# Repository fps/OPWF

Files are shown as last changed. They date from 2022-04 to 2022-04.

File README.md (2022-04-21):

# Introduction

This repository contains firmware for a pickup winder based on a Ramps 1.4 board, RepRapDiscount Full Graphics Smart Controller, a 200 steps per revolution stepper motor, a servo and an Arduino Mega 2560 microcontroller board.

[Video showing the winder in action](https://www.youtube.com/shorts/mcej-a_-2Q8)

# Installation

- Assemble the pickup winder as can be seen in the picture below
- Use e.g. the Arduino IDE to flash the sketch in the src/ directory to the Mega 2560

Assembled winder

# Assembly

- 3d print the motor holder and pickup attachment plate (or think about an alternative way to secure the motor - I successfully used some blocks of wood and some double sided tape)
- Cut a piece of wood to approximately 20 cm by 20 cm that serves as the base
- Mount the arduino Mega 2560 in the back left corner using ca. two wood screws
- Mount the Ramps 1.4 board on top of the Arduino
- Attach at least the Z-direction stepper driver and set it to 4 microsteps using the jumpers before inserting the driver board.
- Set the jumper on the Ramps board to supply 5V power to the servo (That jumper is left of the reset button on the board)
- Attach the servo to the second servo pin from the left (it's the one corresponding to the digital pin D6 - this is important for the PWM and interrupt management)
- Secure the servo cable a little bit with a piece of tape so that it won't entangle with the pickup wire
- Attach the servo on a piece of wood to raise it up a little from the base board. Position it in such a way that the center of the servo axis aligns with the center of a pickup bobbin when attached to the motor
- At the front right attach two felt-padded pieces of wood with 2 screws. These serve as pickup wire tensioner. 
- Figure out a way to connect your stepper motor to the corresponding pins on the Ramps board
- Secure the stepper motor cables with some tape so that they don't entangle with the pickup wire
- Mount the display using two wood screws, but screw them in at an angle. The back of the display will be held by the flat cables.

# Usage

## General

- Press the encoder button on the display to enter/leave a setting
- Rotate the encoder to change a setting. Since the display is so godawfully slow the code waits for a timeout until updating the display.
- Press the STOP button on the display to start the winding process
- Press the STOP button to stop the winding process, too ;)
- Press the STOP button twice (doubleclick) to reset the "Current Winds" counter to 0

## Menu entries

- Target winds: The number of winds that the winder will stop winding at. Note that you can change this at any point. So to wind for e.g. 1000 winds and then another 1000 winds first set the target winds to 1000, start the winding, and after it stopped set the target to 2000 and start the winding again.
- Current winds: The current number of winds performed since the counter was last reset
- Wind direction: Can be either 1 or -1 corresponding to either clockwise/anticlockwise or anticlockwise/clockwise directions depending on how you wired the stepper motor
- Speed W/s: The speed in winds per second
- Acceleration W/s^2: The acceleration used to ramp up to the selected speed
- Winds/Sweep: The number of winds performed for a full servo sweep. So if you select 100 here, the servo will be swept from Right limit to Left limit during the first 50 winds and from Left limit to Right limit during the second 50 sweeps. Then the dance starts all over.
- Right limit deg.: The first servo limit 
- Left limit deg. The second servo limit

# CAVEATS

- The button handling is done purely in software without interrupts, so sometimes presses are missed.

# LICENSE

- To be figured out

# Author

- Florian Paul Schmidt
- Florian Hofmann

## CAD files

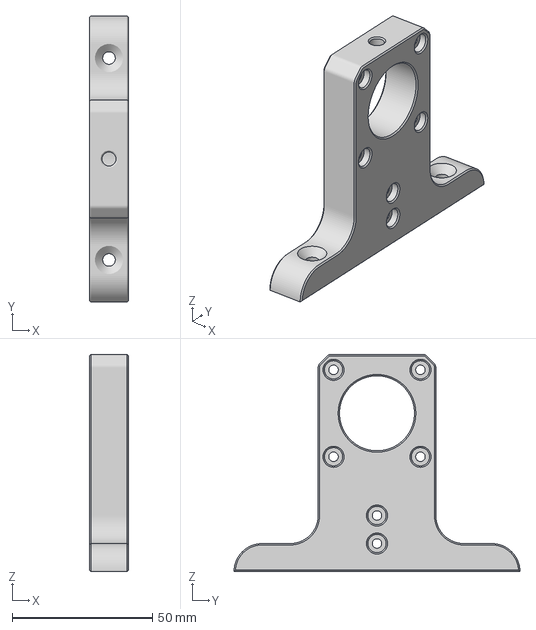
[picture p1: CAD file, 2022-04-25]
hardware/3mf/MotorMount.3mf
14.0 x 102.0 x 77.5 mm

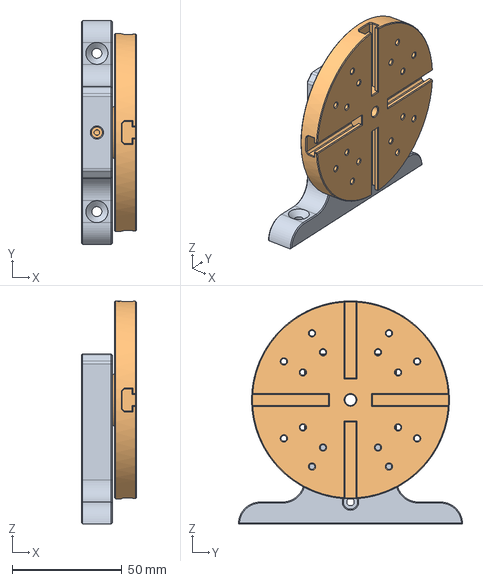
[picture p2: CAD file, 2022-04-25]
hardware/step/Mini-Lathe v3.step
25.0 x 102.0 x 101.5 mm

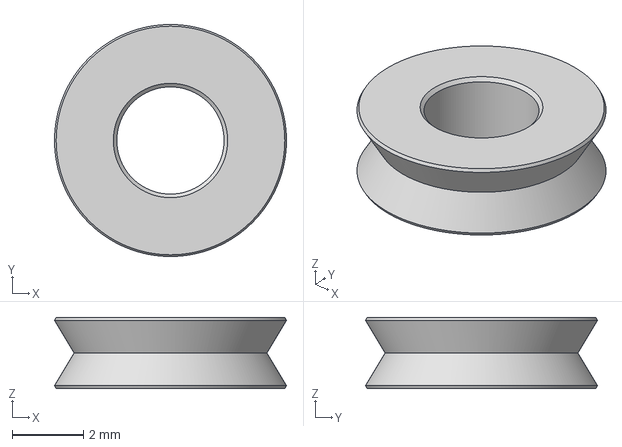
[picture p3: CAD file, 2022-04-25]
hardware/3mf/Guide Ring.3mf
6.50 x 6.50 x 2.00 mm

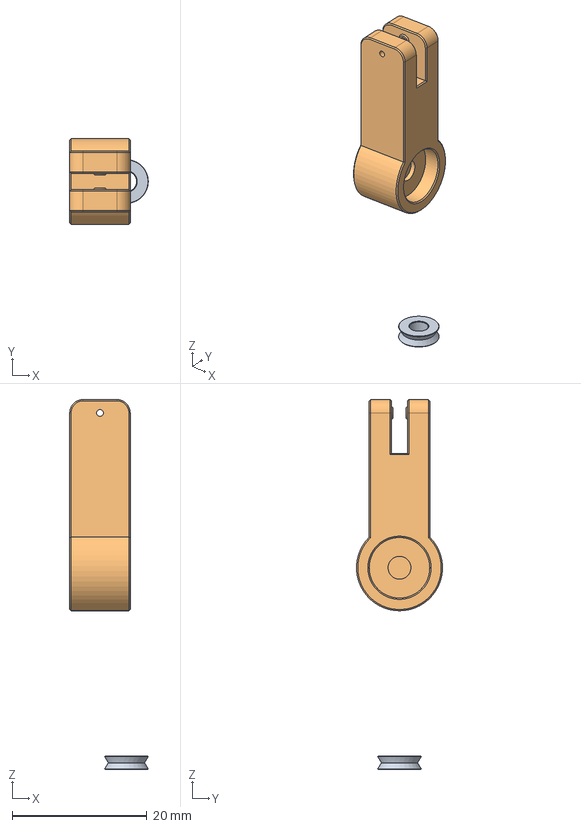
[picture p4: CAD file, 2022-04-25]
hardware/step/Roller v2.step
11.7 x 12.8 x 55.0 mm
Guide Ring
Guide Arm

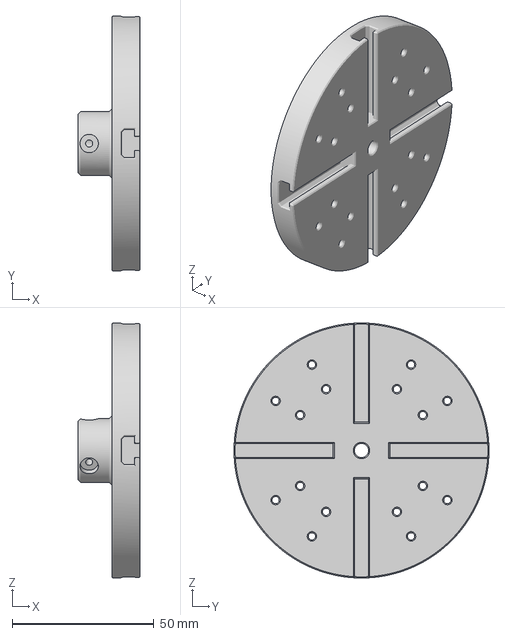
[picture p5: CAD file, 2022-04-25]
hardware/3mf/FrontPlate.3mf
22.0 x 90.0 x 90.0 mm

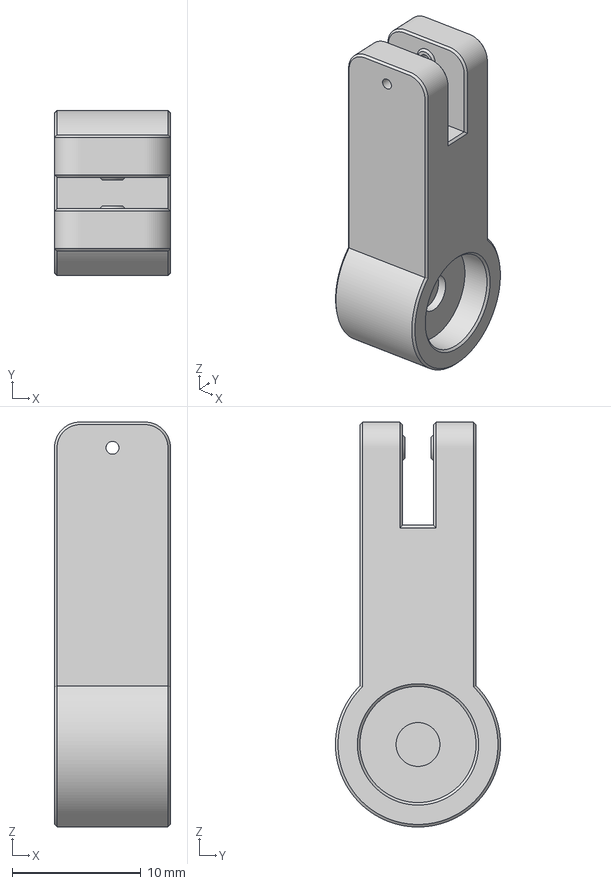
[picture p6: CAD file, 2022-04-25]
hardware/3mf/Guide Arm.3mf
9.00 x 12.8 x 31.4 mm

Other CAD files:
hardware/stl/FrontPlate.stl
hardware/stl/Guide Arm.stl
hardware/stl/Guide Ring.stl
hardware/stl/MotorMount.stl

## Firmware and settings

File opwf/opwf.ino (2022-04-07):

#define ENCODER_USE_INTERRUPTS
#include <EncoderButton.h>

#include <Button2.h>
#include <Servo_Hardware_PWM.h>
#include <EEPROM.h>
#include <U8g2lib.h>

// #################### CONSTANTS

#define STOP_BUTTON 41

#define ENCODER_PUSH_BUTTON 35
#define ENCODER_BUTTON1 31 
#define ENCODER_BUTTON2 33

#define MOTOR_Z_ENABLE 38
#define MOTOR_Z_DIRECTION 55
#define MOTOR_Z_STEP 54

#define SERVO_PIN 6

const long stepper_timer_period_usec = 20L;
const long servo_timer_period_usec = 10e3L;

const long steps_per_turn = 200L;
const long microsteps = 16L;


// #################### GLOBAL STATE

long step_period_usec = 0;
unsigned long steps_per_second;
long elapsed_since_step_usec = 0L;


unsigned long steps_per_second_limit = 1L;
volatile long max_steps = 1L;
volatile long steps_taken = 0L;

// volatile bool start_active = false;
long start_time_usec = 0;


// #################### SERVO

Servo servo;


// #################### BUTTONS

Button2 encoder_push_button;
Button2 stop_button;

volatile enum {
  STOPPED = 0,
  STARTING,
  RUNNING,
  STOPPING
} state;


// #################### MENU

U8G2_ST7920_128X64_F_SW_SPI u8g(U8G2_R0, 23, 17, 16);

struct menu_item {
  const char* text;
  float value;
  float increment;
  float minimum;
  float maximum;
};

enum menu_entry_indices {
  TARGET_WINDS = 0,
  CURRENT_WINDS,
  WIND_DIRECTION,
  SPEED,
  ACCELERATION,
  WINDS_PER_SWEEP,
  RIGHT_LIMIT,
  LEFT_LIMIT,
  NUMBER_OF_MENU_ENTRIES
};

int current_menu_entry_index = 0;
bool menu_needs_redraw = false;

menu_item menu[NUMBER_OF_MENU_ENTRIES] = {
  { "Target Winds     ",    1000,  50,     0, 20000 },
  { "Current Winds    ",       0,   0,     0, 20000 },
  { "Wind Direction   ",       1,   2,    -1,     1 },
  { "Speed W/s        ",       2,   0.1, 0.1,    10 },
  { "Accel. W/s^2     ",     1.0,   0.1, 0.1,    10 },
  { "Winds/Sweep      ",     100,  10,     0,  5000 },
  { "Right limit deg. ",      90,   1,     0,   180 },
  { "Left Limit deg.  ",     120,   1,     0,   180 }
};

bool menu_data_entry_active = false;

EncoderButton encoder(ENCODER_BUTTON1, ENCODER_BUTTON2);

void draw_menu() {
  u8g.firstPage();
  do {
    byte y_position = 7;
    const byte y_spacing = 8;
    u8g.setFont(u8g2_font_5x7_mr);
    for (byte menu_entry_index = 0; menu_entry_index < NUMBER_OF_MENU_ENTRIES; ++menu_entry_index) {  
      u8g.setDrawColor(2);
      if (menu_entry_index == current_menu_entry_index && !menu_data_entry_active) {
        u8g.setDrawColor(0);    
      }
      u8g.setCursor(0, y_position);
      u8g.print(menu[menu_entry_index].text); 
      
      if (menu_entry_index == current_menu_entry_index && menu_data_entry_active) {
        u8g.setDrawColor(0);    
      }
      char buffer[10];
      dtostrf(menu[menu_entry_index].value, 8, 2, buffer);
      u8g.print(buffer);    
      y_position += y_spacing;      
    }
  } while ( u8g.nextPage() );  
}


// #################### EEPROM

const float magic_cookie = 331.337f;

void read_eeprom() {
  Serial.println("Restoring from EEPROM...");
  for (unsigned index = 0; index < NUMBER_OF_MENU_ENTRIES; ++index) {
    EEPROM.get((index+1)*sizeof(float), menu[index].value);
  }
  Serial.println("Done.");
}

void save_eeprom() {
  Serial.println("Saving to EEPROM");
  EEPROM.put(0, magic_cookie);
  float eeprom_value;
  for (unsigned index = 0; index < NUMBER_OF_MENU_ENTRIES; ++index) {
    EEPROM.get((index+1)*sizeof(float), eeprom_value);
    if (eeprom_value != menu[index].value) {
      Serial.println(menu[index].value);
      EEPROM.put((index+1)*sizeof(float), menu[index].value);      
    }
  }
  Serial.println("Done.");
}


// #################### SETUP

void setup() {
  Serial.begin(115200);
  while (!Serial) {}

  Serial.println("Open Pickup Winder Firmware v0.1 starting up...");

  Serial.println("Setting up EEPROM...");
  
  float eeprom_value;
  if (EEPROM.get(0, eeprom_value) == magic_cookie) {
    read_eeprom();
  } else {
    save_eeprom(); 
  }

  Serial.println("Setting up pins...");
  
  pinMode(37, OUTPUT);

  // Encoder buttons
  pinMode(ENCODER_PUSH_BUTTON, INPUT_PULLUP);
  pinMode(ENCODER_BUTTON1, INPUT_PULLUP);
  pinMode(ENCODER_BUTTON2, INPUT_PULLUP);

  pinMode(STOP_BUTTON, INPUT_PULLUP);

  pinMode(MOTOR_Z_ENABLE, OUTPUT);
  pinMode(MOTOR_Z_DIRECTION, OUTPUT);
  pinMode(MOTOR_Z_STEP, OUTPUT);

  digitalWrite(MOTOR_Z_ENABLE, HIGH);

  Serial.println("Setting up buttons...");
  
  stop_button.begin(STOP_BUTTON);
  stop_button.setClickHandler(button_handler);
  stop_button.setDoubleClickHandler(button_handler);
  encoder_push_button.begin(ENCODER_PUSH_BUTTON);
  encoder_push_button.setClickHandler(button_handler);


  Serial.println("Drawing menu...");
  
  u8g.begin();
  draw_menu();

  Serial.println("Setting up servo...");
  
  // Servo
  servo.attach(SERVO_PIN);
  servo.write(menu[LEFT_LIMIT].value);
  // pinMode(SERVO_PIN, OUTPUT);
  // analogWrite(SERVO_PIN, 128);

  // Beeper

  Serial.println("Setting up state...");
  state = STOPPED;
  
  Serial.println("Setting up timers...");

  cli();
  //set timer2 interrupt at 8kHz
  TCCR2A = 0;// set entire TCCR2A register to 0
  TCCR2B = 0;// same for TCCR2B
  TCNT2  = 0;//initialize counter value to 0
  // set compare match register for 8khz increments
  // OCR2A = 249;// = (16*10^6) / (8000*8) - 1 (must be <256)
  OCR2A = 2 * stepper_timer_period_usec - 1;
  // turn on CTC mode
  TCCR2A |= (1 << WGM21);
  // Set CS21 bit for 8 prescaler
  TCCR2B |= (1 << CS21);   
  // enable timer compare interrupt
  TIMSK2 |= (1 << OCIE2A);

  TCCR3A = 0;// set entire TCCR2A register to 0
  TCCR3B = 0;// same for TCCR2B
  TCNT3  = 0;//initialize counter value to 0
  // set compare match register for 8khz increments
  // OCR2A = 249;// = (16*10^6) / (8000*8) - 1 (must be <256)
  OCR3A = (servo_timer_period_usec / 4) - 1;
  // OCR3A = 10;
  // turn on CTC mode
  // TCCR3A |= (1 << WGM31);
  TCCR3B |= (1 << WGM32);
  // Set CS21 bit for 8 prescaler
  TCCR3B |= (1 << CS31);   
  TCCR3B |= (1 << CS30);   
  // enable timer compare interrupt
  TIMSK3 |= (1 << OCIE3A);
  sei();
  
  Serial.println("Startup done.");
}


// #################### INTERRUPTS

// void process() {
ISR(TIMER2_COMPA_vect) {
  cli();
  if (state != STOPPED) {
    if (steps_taken < max_steps) {
      if (elapsed_since_step_usec > step_period_usec) {
        elapsed_since_step_usec -= step_period_usec;
    
        PORTF |= B00000001;
        PORTF &= B11111110;
      
        ++steps_taken;
      }
    } else {
      state = STOPPING;
    }
  }
  elapsed_since_step_usec += stepper_timer_period_usec;
  sei();
}

volatile long servo_timer_interrupts = 0;

ISR(TIMER3_COMPA_vect) {
  cli();
  if (state != STOPPED) {
    step_period_usec = 1e6L / steps_per_second;

    const float current_wind = (float)steps_taken / (float)(steps_per_turn * microsteps);
    const float sweep_phase = fmodf(current_wind / menu[WINDS_PER_SWEEP].value, 1.0);
    // Serial.println(sweep_phase);
    if (sweep_phase < 0.5f) {
      const float half_phase = 2.0f * sweep_phase;
      servo.write((menu[LEFT_LIMIT].value - menu[RIGHT_LIMIT].value) * half_phase + menu[RIGHT_LIMIT].value);
    } else {
      const float half_phase = 2.0f * (sweep_phase - 0.5f);
      servo.write((menu[RIGHT_LIMIT].value - menu[LEFT_LIMIT].value) * half_phase + menu[LEFT_LIMIT].value);
    }
    
  }
  ++servo_timer_interrupts;
  sei();
}
// #################### BUTTON HANDLING

unsigned long last_output_usec = 0;
const unsigned long output_period_usec = 2e6L;

int last_encoder_position = 0;
unsigned long last_encoder_change_usec = 0;

volatile unsigned long now_usec = 0;

void button_handler(Button2 &button) {
  if (button == stop_button) {
      if (button.getClickType() == SINGLE_CLICK) {
        save_eeprom();
        start_time_usec = now_usec;
        steps_per_second_limit = menu[SPEED].value * steps_per_turn * microsteps;
        max_steps = menu[TARGET_WINDS].value * steps_per_turn * microsteps;
        step_period_usec = 1e6L;
        elapsed_since_step_usec = 0;

        Serial.print("limit: "); Serial.println(steps_per_second_limit); 

        if (state == STOPPED) {
          Serial.println("STOPPED -> STARTING...");
          digitalWrite(MOTOR_Z_ENABLE, LOW);
          if (menu[WIND_DIRECTION].value > 0) digitalWrite(MOTOR_Z_DIRECTION, HIGH); else digitalWrite(MOTOR_Z_DIRECTION, LOW);
          state = STARTING;
          return;
        }

        if (state == RUNNING) {
          Serial.println("RUNNING -> STOPPING...");
          state = STOPPING;
          return;
        }

        if (state == STARTING) {
          Serial.println("STARTING -> STOPPING...");
          state = STOPPING;
          return;
        }
      }

      if (button.getClickType() == DOUBLE_CLICK) {
        menu[CURRENT_WINDS].value = 0;
        steps_taken = 0;
        draw_menu();
        return;
      }
  }

  if (button == encoder_push_button) {
    menu_data_entry_active = !menu_data_entry_active;
    draw_menu();
  }
}


// #################### MAIN LOOP

void loop() {
  now_usec = micros();
  encoder.update();
  stop_button.loop();
  encoder_push_button.loop();
  
  // STEPPER CONTROL

  if (state == STOPPING) {
      Serial.println("STOPPING -> STOPPED...");
      digitalWrite(MOTOR_Z_ENABLE, HIGH);
      state = STOPPED;
      menu[CURRENT_WINDS].value = (float)steps_taken / (steps_per_turn * microsteps);
      draw_menu();
      Serial.println("Done.");
  }
  
  if (state == STARTING) {
    const float seconds_since_start = (now_usec - start_time_usec) / 1e6f;
    float winds_per_second = menu[ACCELERATION].value * seconds_since_start;
    if (winds_per_second > menu[SPEED].value) winds_per_second = menu[SPEED].value;
    
    // steps_per_second = microsteps * (10L + ((now_usec - start_time_usec) / 10000L));
    steps_per_second = 10L + winds_per_second * microsteps * steps_per_turn;
    // steps_per_second = 5L;
    if (steps_per_second > steps_per_second_limit) {
      steps_per_second = steps_per_second_limit;
      Serial.println("STARTING -> RUNNING");
      state = RUNNING;
    }
  }

  if (state != STOPPED) {
    step_period_usec = 1e6L / steps_per_second;
  }

  // MENU
  
  const int encoder_position = encoder.position();
  if (encoder_position != last_encoder_position) {
    if (menu_data_entry_active) {
      int delta = encoder_position - last_encoder_position;
      menu[current_menu_entry_index].value += menu[current_menu_entry_index].increment * delta;
      if (menu[current_menu_entry_index].value > menu[current_menu_entry_index].maximum) menu[current_menu_entry_index].value = menu[current_menu_entry_index].maximum;
      if (menu[current_menu_entry_index].value < menu[current_menu_entry_index].minimum) menu[current_menu_entry_index].value = menu[current_menu_entry_index].minimum;
    } else {
      current_menu_entry_index += encoder_position - last_encoder_position;
      if (current_menu_entry_index < 0) current_menu_entry_index += NUMBER_OF_MENU_ENTRIES;
      current_menu_entry_index %= NUMBER_OF_MENU_ENTRIES;
      /*
      if (current_menu_entry_index < 0) current_menu_entry_index = 0;
      if (current_menu_entry_index > (NUMBER_OF_MENU_ENTRIES - 1)) current_menu_entry_index = (NUMBER_OF_MENU_ENTRIES - 1);
      */
    }
    last_encoder_change_usec = now_usec;
    menu_needs_redraw = true;
    last_encoder_position = encoder_position;
  }
  
  if (menu_needs_redraw && now_usec - last_encoder_change_usec > 2e5L)
  {
    draw_menu();
    menu_needs_redraw = false;
  }

  // DEBUG OUTPUT
  
  if (true && now_usec - last_output_usec > output_period_usec) {
    last_output_usec = now_usec;

    Serial.print(" enc pos: ");
    Serial.print(encoder.position());
    Serial.print(" enc push: ");
    Serial.print(digitalRead(ENCODER_PUSH_BUTTON));
    Serial.print(" stop: ");
    Serial.print(digitalRead(STOP_BUTTON));
    Serial.print(" winds: ");
    Serial.print((float)steps_taken / (steps_per_turn * microsteps));
    Serial.print(" steps: ");
    Serial.print(steps_taken);
    Serial.print(" sps: ");
    Serial.print(steps_per_second);
    Serial.print(" step period: ");
    Serial.print(step_period_usec);
    Serial.print(" servo irqs: ");
    Serial.print(servo_timer_interrupts);
    Serial.println("");
    
    menu[CURRENT_WINDS].value = (float)steps_taken / (float)(steps_per_turn * microsteps);
    draw_menu();
  }  

  return;
}

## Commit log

2022-03-01 - use Button2 to simplify logc - work on smoothing the start
2022-04-03 - added eeprom stuff, servo stuff
2022-04-04 - use timer2 for stepper control
2022-04-05 - stupid bug - enforce limits
    [sketch_feb21a.ino]
2022-04-05 satisfying the arduino ide
2022-04-06 - use hardware PWM servo library
2022-04-07 - use a different interrupt for pwm and servo loop
2022-04-07 - fix servo control period
    [opwf.ino]
2022-04-07 output current winds during winding
2022-04-07 add some assembly instructions
2022-04-20 - add photo of assembled system
2022-04-21 add comment about servo power
2022-04-24 models for 3d printing + step files for modification
    [FrontPlate.3mf, Guide Arm.3mf, Guide Ring.3mf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]
2022-04-24 github does not like 3mf, added stls too
    [FrontPlate.3mf, FrontPlate.stl, Guide Arm.3mf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]
